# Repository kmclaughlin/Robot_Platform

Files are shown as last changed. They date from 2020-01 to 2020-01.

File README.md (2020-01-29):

# Robot Platform
 A simple robot platform with the basic components for motion. Designed for easy expansion with additional sensors and peripherals

## Aim
The aim of this project is to design an open source robot to help teach people robotics that is:

1. relatively cheap and easy to build
1. easy to modify, expand and iterate on
1. capable of a variety of tasks

These goals drove design choices such as choosing certain components over others in an effort to keep the build process simple and the barriers to entry low

# Whats in this Repo?
1. STL files for the current version of the robot.  
1. STL files for various sensor mounts and expansions.  
1. Arduino code for simple PWM based movement.  
1. Arduino example code for wall following and line following.  
1. Arduino code for advanced encoder based movement.

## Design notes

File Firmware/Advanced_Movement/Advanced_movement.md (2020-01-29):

# Advanced Movement Explanation
## What is the problem with basic movement?
The basic robot movement uses PWM to control the motor speed. This method is relatively straight forward but it has its problems. 

The underpinning issue with using PWM alone for speed control is that this is an open loop control method, i.e. there is no feedback to the micro-controller of the action it has asked for. This causes a variety of problems. 

PWM in this case is acting like a digital to analog converter. The pulsed output has a time averaged value equivalent to some DC voltage between 0V and maxV. Low PWM values are therefore like low voltages to the motor and if the voltage is too low it is unable to overcome the resistance of the motor/friction with the ground/momentum of the motor and will not move. That is until it can overcome it and it starts moving relatively quickly. 

This dead-zone between 0RPM and minRPM makes it difficult to make the robot move slowly in a controlled fashion. Additionally due to differences inherent to each motor, unbalanced weight distribution of the robot, a surface with a varying coefficient of friction etc the same PWM value to 2 different motors will not result in the same speed. Therefore it is difficult to make the robot go in a straight line (or do anything consistently)

## How it is solved
The first thought might be to try and fix the problem in software with a variety of coefficients for different situations to account for the differences in motor response or other problems. However this is often not the best approach. A robot is not a system of hardware and a separate system of software. A robot is combination of both these fields and often a problem that can be solved with a great deal of effort, thought and complexity in software can be solved much more easily (and more effectively) with a combined software and hardware approach.

In this case encoders are added to the robot to close the control loop. That is when the arduino asks the motors to move at a certain speed the encoders tell the arduino what the motors actually did. The arduino can then adjust what it tells the motors to do. An additional benefit of closing this control loop to track motor speed is that we can also track how far the motor has moved, which may be useful for future tasks.

## Speed Control with Encoders - TODO

```c++
void setup() {
  // Timer interrupt setup
  OCR0A = 0xAF; // set the compare register A for timer0
  TIMSK0 |= _BV(OCIE0A);  //enable the compare interrupt A for timer 0

  //continue setup
}
```

```c++
// motor control interrupt service routine
ISR(TIMER0_COMPA_vect) {
  //alternate left and right motor control to reduce processor load.
  //therefore each motor updates every 2ms
  if (motorControlFlag) {
  //left motor
    long encoderReading = leftEncoder.read();
    long measuredSpeed = abs(leftEncoderStore - encoderReading) * 15; 
    leftEncoderStore = encoderReading;
    if (measuredSpeed > leftMotorSpeed)
      digitalWrite(L_MOTOR_ENABLE, LOW);
    else
      digitalWrite(L_MOTOR_ENABLE, HIGH);
  }
  else {
  //right motor
    long encoderReading = rightEncoder.read();
    long measuredSpeed = abs(rightEncoderStore - encoderReading) * 15; 
    rightEncoderStore = encoderReading;
    if (measuredSpeed > rightMotorSpeed)
      digitalWrite(R_MOTOR_ENABLE, LOW);
    else
      digitalWrite(R_MOTOR_ENABLE, HIGH);
  }
  motorControlFlag = !motorControlFlag;
}
```

## Useful Links for More About Interrupts
https://learn.adafruit.com/multi-tasking-the-arduino-part-2/timers  
https://www.teachmemicro.com/arduino-timer-interrupt-tutorial/  
https://arduino.stackexchange.com/questions/30968/

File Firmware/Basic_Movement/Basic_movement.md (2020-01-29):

# Basic Robot Movement
## Motor Driver
### What is a motor driver for?
The arduino can't provide the voltage and current required to power the motor directly. The arduino pins can't provide (source) or take (sink) that much current, trying to run a motor directly from the arduino can damage it! The arduino is also limited to 5V which may be lower than desired for the motors. The motor driver is the interface between the power source an the motors that allow the arduino to control the motor direction and speed.
### How does a motor driver work?
When a voltage is applied to the terminals of a DC motor it rotates. To make it rotate the opposite direction the wires need to be switched to make the current flow the other way. To achieve this without having to physically switching the wires, transistors are used. Transistors set up in a configuration known as a H-bridge allow the the direction of current through a motor to be changed.

This image gives a simplified diagram of the H-bridge in the motor driver https://i.stack.imgur.com/aS6V5.jpg

A left direction pin controls the left switches. When `HIGH` top left is closed and bottom left is open. The same is true for the right direction pin for the right switches. So to drive the motor set leftDir to `HIGH` and rightDir to `LOW`. To reverse the direction set leftDir to `LOW` and rightDir to `HIGH`. So using two digital pins the motor direction can be controlled.

This gives the motor 3 states; off, full forward, full reverse. The speed of the motor can be controlled with a pwm signal to the enable switch at the bottom. (more on pwm speed control below). 

Therefore the motor needs 1 pwm pin and 2 digital pins to fully control it.
There are ways to control the speed and direction of the motor using 1 pwm pin and 1 digital pin, or even with 1 pwm pin and a NOT gate. If you are running out of pins on the uno this could be a simple way to free up some space.

### Speed Control with PWM
PWM stands for pulse width modulation. A digital pin is pulsed `HIGH` and `LOW` quickly at a fixed rate with the width of each pulse being changed depending on the desired output. Trivially when the pulse width is 0 (0% duty cycle) the digital pin is off completely and when the pulse width is max (100% duty cycle) the pin is on completely. At different duty cycles in between the output provides an averaged voltage between 0-100%. Therefore the PWM signal acts like a digital to analog converter, when the motor is given a lower duty cycle pwm input it turns slower as if it were being driven with a lower voltage.

The arduino only has a few pins capable of PWM these are marked on the board with a `~` symbol

## Motor Driver Function
This example left motor function takes care of motor control so you never need to address the motor pins directly, just call this function. Send it a speed value between -255 and 255 and the motor will go from full reverse to full forward.
```c++
void driveLeftMotor(int speed){
  analogWrite(L_MOTOR_ENABLE, abs(speed));
  if (speed > 0){
    digitalWrite(L_MOTOR_1, HIGH);
    digitalWrite(L_MOTOR_2, LOW);
  }
  else{
    digitalWrite(L_MOTOR_1, LOW);
    digitalWrite(L_MOTOR_2, HIGH);
  }
}
```
## Troubleshooting
The robot is circular so you many end up redefining which way is "forward". Doing this is an issue because it inverts the direction of the motors but it also switches left and right. This can be fixed by switching the pin definitions for the motors at the top of the file. Do it slowly and check one motor at a time that it drives forward and reverse as expected.

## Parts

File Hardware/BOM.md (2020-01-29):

| Component | Price | Qty | Total  | Link |
|---|---|-----|---|---|
| Elegoo Uno | £7.99 | 1 | £7.99  | https://www.amazon.co.uk/Elegoo-Board-ATmega328P-ATMEGA16U2-Arduino-x/dp/B01EWOE0UU/ |
| Expansion board | £9.29 | 1 | £9.29  | https://www.robotshop.com/uk/gravity-i-o-expansion-shield-arduino-v7.html |
| Geared motor with encoder  | £7.61 | 2 | £15.22 | https://www.robotshop.com/uk/micro-6v-160rpm-1201-dc-geared-motor-encoder.html |
| 12mm rubber tyres | £4.00 | 2 | £7.99  | https://www.amazon.co.uk/gp/product/B01KKBLXR2 |
| L298N motor driver | £2.40 | 1 | £2.40  | https://www.amazon.co.uk/TIMESETL-Stepper-Controller-Electric-Projects/dp/B077YC3JX9 |
| Battery individual 2600mAh | £7.82 | 2 | £15.64 | https://uk.rs-online.com/web/p/speciality-size-rechargeable-batteries/8801558/ |
| Power switch | £3.60 | 1 | £3.60  | http://www.hobbytronics.co.uk/mosfet-power-switch-sv-rev |
| 15mm Ball Bearing | £0.70 | 2 | £1.40  | https://www.amazon.co.uk/ueetek-10-pieces-Diameter-Carbon-Bearing/dp/B0795MND8G/ |
| Wheel | £5.15 | 1 | £5.15  | https://www.robotshop.com/uk/tamiya-wheels-pair.html |
| Ultrasonic sensor | £0.84 | 3 | £2.52  | https://www.amazon.co.uk/HC-SR04-Ultrasonic-Distance-Rangefinder-Detection/dp/B0066X9V5K/ |

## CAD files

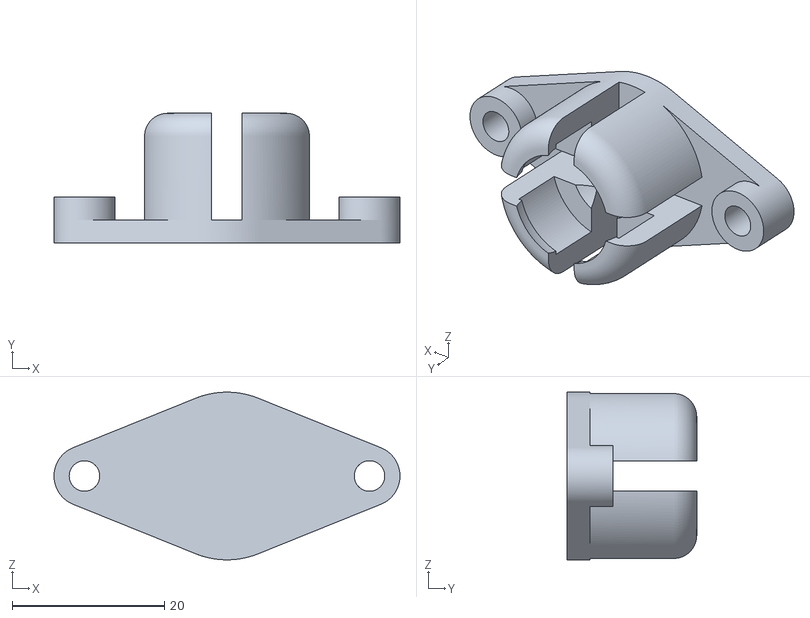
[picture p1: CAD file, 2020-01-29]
Hardware/STL_Files/Main_Chassis/ball_bearing_mount.stl
45.4 x 17.0 x 22.0

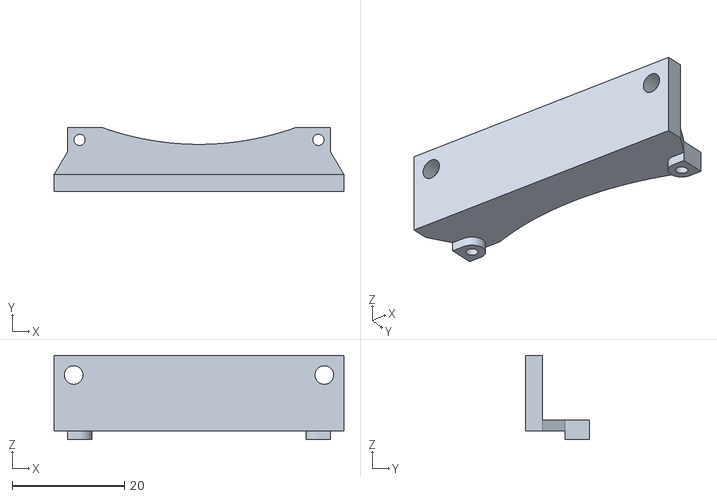
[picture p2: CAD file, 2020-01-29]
Hardware/STL_Files/Sensor_Mounts/front_ultrasound.stl
51.6 x 11.4 x 15.0

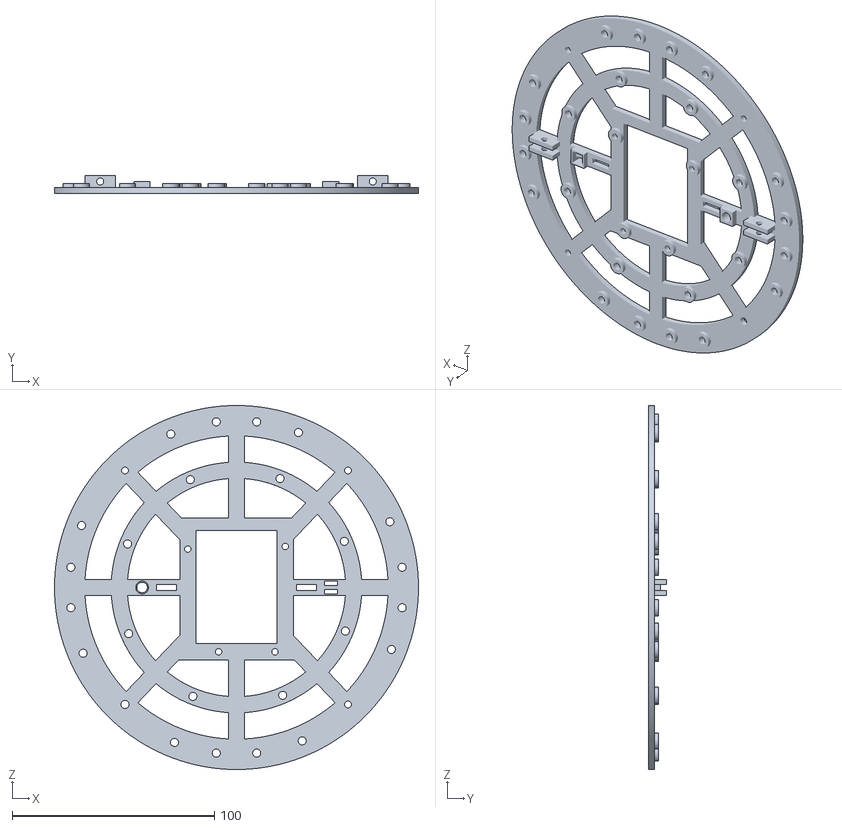
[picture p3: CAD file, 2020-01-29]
Hardware/STL_Files/Main_Chassis/chassis_top.stl
180.0 x 9.00 x 180.0

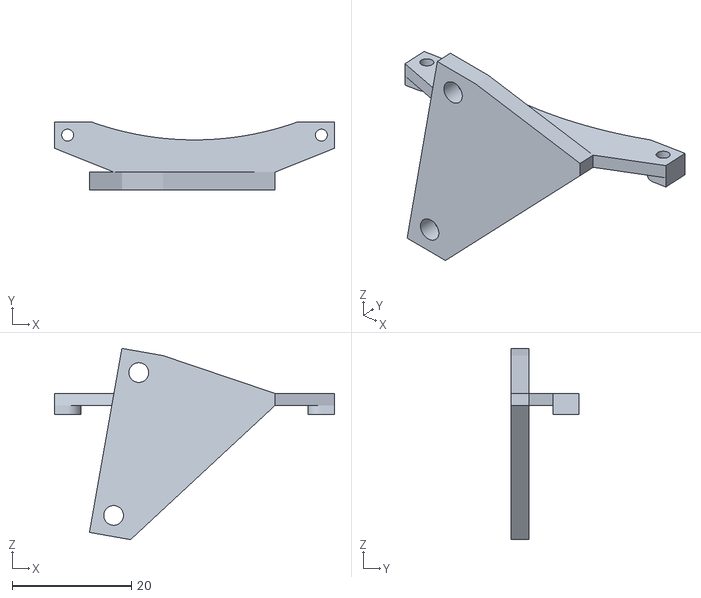
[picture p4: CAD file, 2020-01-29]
Hardware/STL_Files/Sensor_Mounts/side_ultrasound.stl
46.9 x 11.4 x 32.0

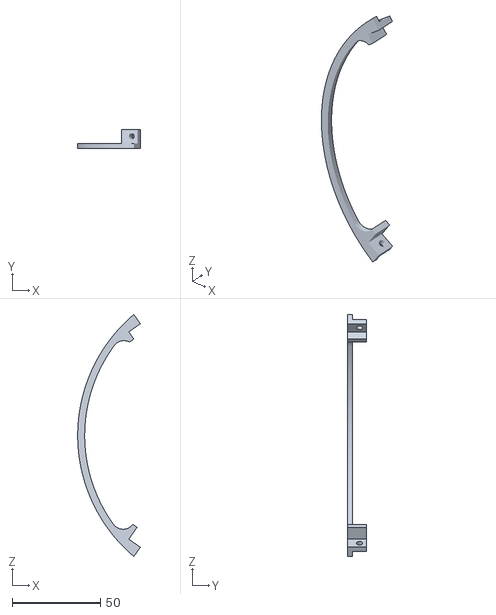
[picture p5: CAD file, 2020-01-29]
Hardware/STL_Files/Main_Chassis/wheel_guard_left.stl
35.6 x 11.0 x 137.5

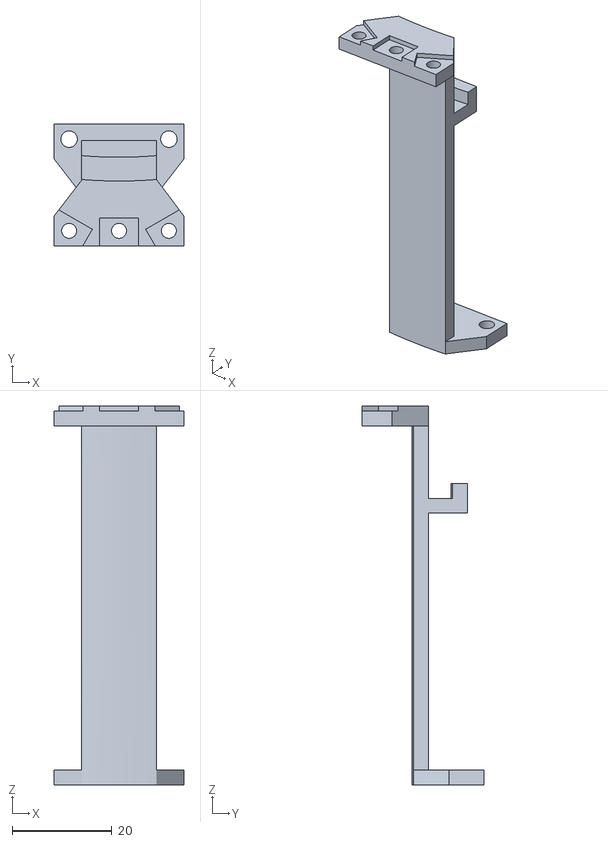
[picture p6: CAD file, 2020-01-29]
Hardware/STL_Files/Sensor_Mounts/line_following_module.stl
26.0 x 24.4 x 76.0

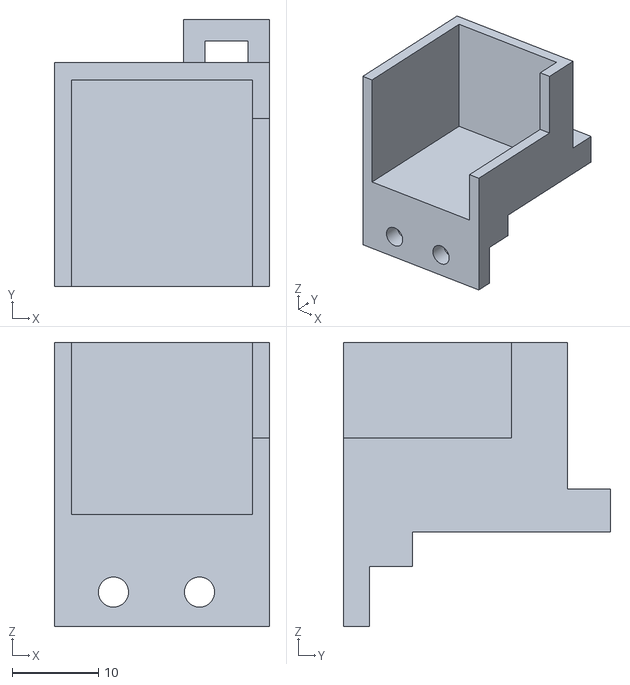
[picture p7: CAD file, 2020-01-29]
Hardware/STL_Files/Main_Chassis/top_encoder_cover_left.stl
25.0 x 31.0 x 33.0

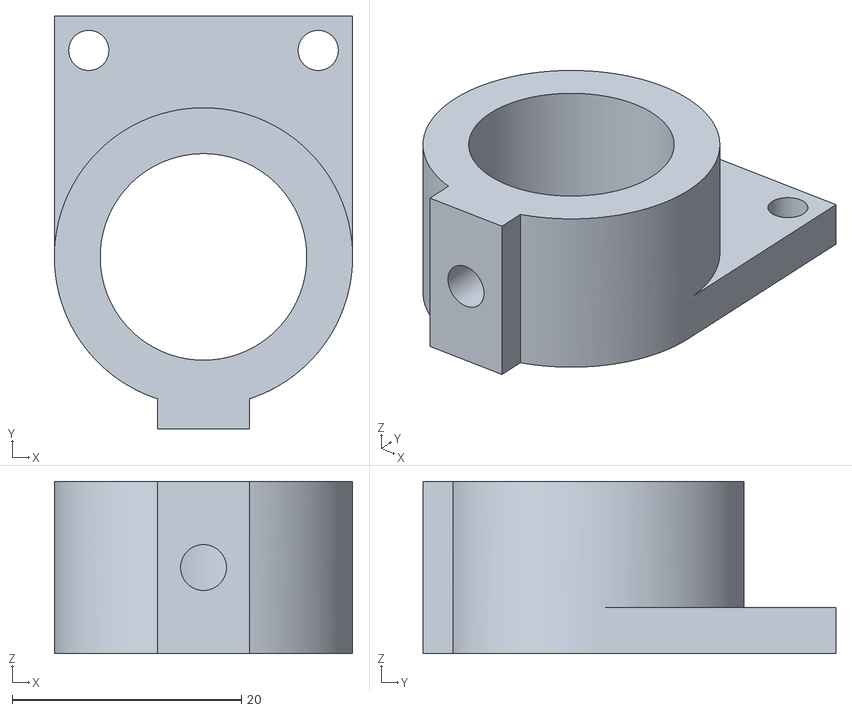
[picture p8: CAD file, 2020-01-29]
Hardware/STL_Files/Sensor_Mounts/pen_holder.stl
26.0 x 36.0 x 15.0

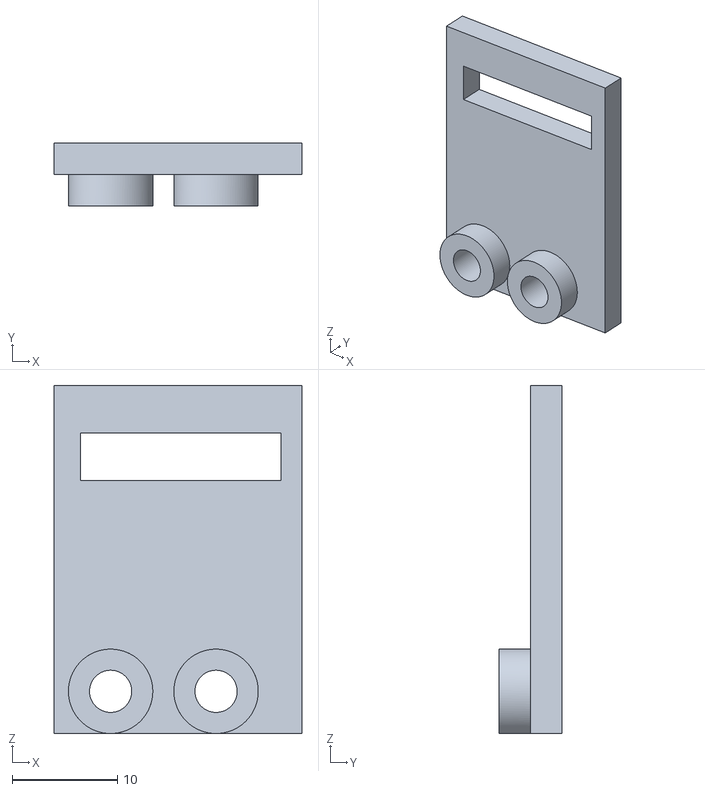
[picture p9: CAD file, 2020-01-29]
Hardware/STL_Files/Main_Chassis/bottom_encoder_cover_left.stl
23.5 x 6.00 x 33.0

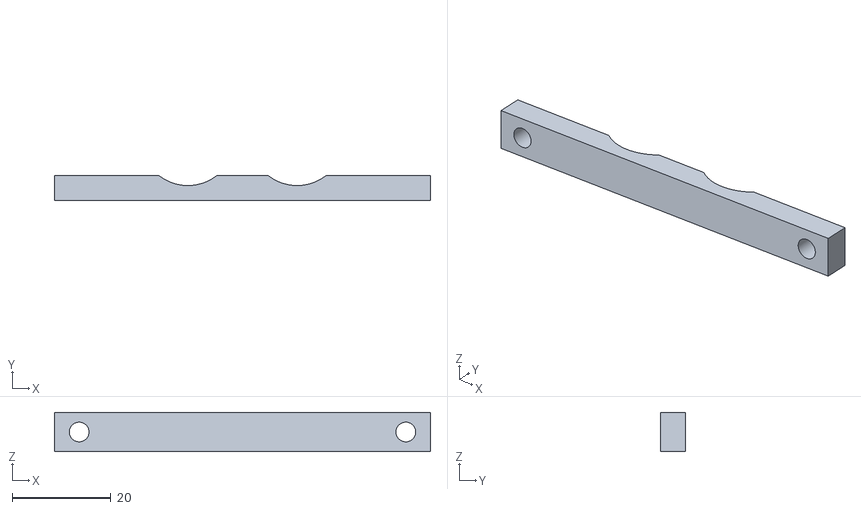
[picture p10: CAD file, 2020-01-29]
Hardware/STL_Files/Main_Chassis/battery_bar.stl
76.2 x 5.00 x 8.00

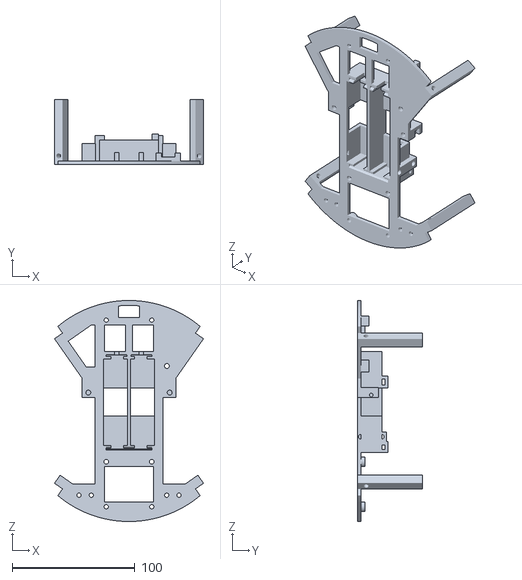
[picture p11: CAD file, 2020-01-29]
Hardware/STL_Files/Main_Chassis/chassis_base.stl
121.4 x 53.0 x 180.0

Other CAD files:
Hardware/STL_Files/Main_Chassis/top_encoder_cover_right.stl
Hardware/STL_Files/Sensor_Mounts/side_ultrasound_mirror.stl
Hardware/STL_Files/Main_Chassis/wheel_guard_right.stl
Hardware/STL_Files/Main_Chassis/bottom_encoder_cover_right.stl

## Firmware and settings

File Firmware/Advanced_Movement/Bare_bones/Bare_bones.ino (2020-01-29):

#include <Encoder.h>

//Motor pins
#define L_MOTOR_1 11
#define L_MOTOR_2 9
#define L_MOTOR_ENABLE 6
#define R_MOTOR_1 8
#define R_MOTOR_2 7
#define R_MOTOR_ENABLE 5

//encoders
// NOTE don't read from these!
// use the encoder store values below
Encoder leftEncoder(3, 4);
Encoder rightEncoder(2, 10);

volatile long leftEncoderStore = 0, 
  rightEncoderStore = 0;
volatile int rightMotorSpeed = 0,
  leftMotorSpeed = 0;
bool motorControlFlag = false;

// The motor speed is controlled in an ISR at the bottom of
// the file. You can ignore it if you want

void setup() {
  /*------------------------------------------------------------*/
  /*              Interrupt stuff - You can ignore              */
  /*------------------------------------------------------------*/
  /**/  OCR0A = 0xAF; // set the compare register A for timer0
  /**/  TIMSK0 |= _BV(OCIE0A);  //enable the compare interrupt A for timer 0
  /*------------------------------------------------------------*/
  
  Serial.begin(9600);
  //setup motors
  pinMode(L_MOTOR_1, OUTPUT);
  pinMode(L_MOTOR_2, OUTPUT);
  pinMode(R_MOTOR_1, OUTPUT);
  pinMode(R_MOTOR_2, OUTPUT);
  pinMode(L_MOTOR_ENABLE, OUTPUT);
  pinMode(R_MOTOR_ENABLE, OUTPUT);
}

void loop() {
  //YOUR CODE HERE
}

//Put you new functions here


//MOTOR FUNCTIONS
void driveLeftMotor(int speed){
  leftMotorSpeed = abs(speed);
  if (speed > 0){
    digitalWrite(L_MOTOR_1, HIGH);
    digitalWrite(L_MOTOR_2, LOW);
  }
  else{
    digitalWrite(L_MOTOR_1, LOW);
    digitalWrite(L_MOTOR_2, HIGH);
  }
}

void driveRightMotor(int speed){
  rightMotorSpeed = abs(speed);
  if (speed > 0){
    digitalWrite(R_MOTOR_1, LOW);
    digitalWrite(R_MOTOR_2, HIGH);
  }
  else {
    digitalWrite(R_MOTOR_1, HIGH);
    digitalWrite(R_MOTOR_2, LOW);
  }
}

/*------------------------------------------------------------*/
/*                    YOU CAN IGRNORE THIS                    */
/*------------------------------------------------------------*/
/**/  // motor control interrupt service routine
/**/  ISR(TIMER0_COMPA_vect) {
/**/    //alternate left and right motor control to reduce processor load.
/**/    //therefore each motor updates every 2ms
/**/    if (motorControlFlag) {
/**/    //leftMotor
/**/      long encoderReading = leftEncoder.read();
/**/      //TODO fix these magic 15s
/**/      long measuredSpeed = abs(leftEncoderStore - encoderReading) * 15; 
/**/      leftEncoderStore = encoderReading;
/**/      if (measuredSpeed > leftMotorSpeed)
/**/        digitalWrite(L_MOTOR_ENABLE, LOW);
/**/      else
/**/        digitalWrite(L_MOTOR_ENABLE, HIGH);
/**/    }
/**/    else {
/**/    //rightMotor
/**/      long encoderReading = rightEncoder.read();
/**/      //TODO fix these magic 15s
/**/      long measuredSpeed = abs(rightEncoderStore - encoderReading) * 15; 
/**/      rightEncoderStore = encoderReading;
/**/      if (measuredSpeed > rightMotorSpeed)
/**/        digitalWrite(R_MOTOR_ENABLE, LOW);
/**/      else
/**/        digitalWrite(R_MOTOR_ENABLE, HIGH);
/**/    }
/**/    motorControlFlag = !motorControlFlag;
/**/  }
/*------------------------------------------------------------*/

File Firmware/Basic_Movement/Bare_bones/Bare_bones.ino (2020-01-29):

//Motor pins
#define L_MOTOR_1 7
#define L_MOTOR_2 8
#define L_MOTOR_ENABLE 5
#define R_MOTOR_1 9
#define R_MOTOR_2 11
#define R_MOTOR_ENABLE 6

void setup() {
  Serial.begin(9600);
  //setup left motor
  pinMode(L_MOTOR_1, OUTPUT);
  pinMode(L_MOTOR_2, OUTPUT);
  pinMode(L_MOTOR_ENABLE, OUTPUT);
  //setup right motor
  pinMode(R_MOTOR_1, OUTPUT);
  pinMode(R_MOTOR_2, OUTPUT);
  pinMode(R_MOTOR_ENABLE, OUTPUT);
}

void loop() {
  //YOUR CODE HERE
}

//Put you new functions here


//MOTOR FUNCTIONS
void driveLeftMotor(int speed){
  analogWrite(L_MOTOR_ENABLE, abs(speed));
  if (speed > 0){
    digitalWrite(L_MOTOR_1, HIGH);
    digitalWrite(L_MOTOR_2, LOW);
  }
  else{
    digitalWrite(L_MOTOR_1, LOW);
    digitalWrite(L_MOTOR_2, HIGH);
  }
}

void driveRightMotor(int speed){
  analogWrite(R_MOTOR_ENABLE, abs(speed));
  if (speed > 0){
    digitalWrite(R_MOTOR_1, LOW);
    digitalWrite(R_MOTOR_2, HIGH);
  }
  else {
    digitalWrite(R_MOTOR_1, HIGH);
    digitalWrite(R_MOTOR_2, LOW);
  }
}
